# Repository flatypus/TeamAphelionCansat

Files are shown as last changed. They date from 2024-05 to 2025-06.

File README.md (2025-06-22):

# Team Aphelion CanSat | 🏆 1st Place in Canada 2024 | Represented Canada at European Space Agency

## Project repo for Eric Hamber Secondary School from Vancouver, Canada.
### 





### Team Members:
- [Jason Huang](https://www.linkedin.com/in/jason-huang-342449250/) - Co-Captain and Lead Engineer
  - Electrical Design Lead
  - PCB Design and Assembly
  - Mechanical Design and Fabrication
  - CanSat Integration
- [Tristan Yan-Klassen](https://www.linkedin.com/in/tristan-yan-klassen-510788275/) - Co-Captain and Mission Leader
  - Mechanical Design and Fabrication Lead
  - Drilling Apparatus Design and Assembly
  - CanSat Body and Systems Integration
- [Hinson Chan](https://github.com/flatypus) - Software Lead
  - Ground Station Software
  - Map Library Development
  - Website Development
- [John Xu](https://youtube.com/@ibuildstuff) - Hardware Lead
  - Landing Apparatus
  - Soil Sample Intake
  - Ground Station Hardware
- [Anthony Lu](https://www.linkedin.com/in/anthony-lu-026628241/) - External Communications
  - Outreach
  - Parachute Testing
- Mendel Rieseberg - Ground Control
  - Radio Communications

### Project abstract

The goal of CanSat is to design and build a small satellite that fits inside a 330mL soda can. The satellite will be launched to an altitude of 1km and will be deployed to land safely on the ground. We must equip the satellite with sensors to measure temperature, pressure, altitude, and location.

### This Repository

The project is split into six subdirectories:
- 'backend': The backend server for the ground station
- 'mission-control': The frontend dashboard for the ground station
- 'landing': The landing page for the website
- 'embedded': The Arduino code for the CanSat microcontroller
- 'electrical': The electrical schematics and PCB manufacturing files
- 'mechanical': The CAD files of our CanSat

The embedded code consists of sensors detecting temperature, pressure, altitude, and location. The data is sent to the ground station via radio communication, which is relayed via socket communication to the frontend dashboard. The dashboard then visualizes that information in the form of graphs, a map showing the CanSat's location, and the live 3D rotation of the CanSat.

## Project Presentation

This CanSat is designed to complete the primary mission, which is to send temperature and pressure data to the ground station live, at least once a second via radio. The CanSat also has a secondary mission, which is to drill into soil, take a soil sample, and test it with a ninhydrin chemical test within the CanSat's internal chamber. Using the CanSat's FPV live camera, we will determine the presence of amino acids in the soil if a change of color is shown in the ninhydrin.

To accomplish this, the CanSat will be first launched in a rocket to around 1km, then deployed with a parachute to descend at around 6m/s. When the CanSat lands, it will be on its side; we will send a command through our ground station to release the landing legs, which will spring the CanSat upright. We will then initiate the drill, which will drill a hole through our waterproof water chamber, releasing the water onto the soil to dampen it. The CanSat will then continue drilling into the soil, picking up a sample of wet soil, and then stop drilling and retracting up into the CanSat body. The ninhydrin chamber will swivel into place, where then the drill will lower into the chemical, allowing the soil to begin the chemical test. All of this will be remotely controlled from our dashboard.

### Mechanical Design
- Designed in SolidWorks and 3D printed by Tristan, Jason, and John. 
- Custom drill bit and other parts machined to fit inside the CanSat body.
- 4 motors used: GB 2208 Gimbal motor for drilling, 5g servo for testing chamber, N20 worm gear motor for leg release, and 2.5g servo for lead screw.



### Custom Designed Printed Circuit Board
- Designed and hand-assembled by Jason on KiCad.
- Onboard sensors: GPS, 6 axis IMU, and 2 redundant barometers.
- Includes MOSFETs for motor control, 5V buck converter, and TVS diodes for ESD protection.



### Software/Ground Control
- CanSat onboard programming written in Arduino
  - Written for Teensy 4.0, so it supports 'multithreading' (with careful process jumping)
- Nextjs frontend + ExpressJS backend, written by Hinson
  - Data path: Onboard sensors -> Arduino serial -> Radio -> WebSocket backend -> Nextjs graph
- Graphs showing live data updates (temperature, pressure, calculated altitude)
- Fully-functional offline (no WIFI) slippy map
  - Open-sourced [here](https://github.com/flatypus/react-offline-maps) and [npm](https://www.npmjs.com/package/react-offline-maps)
  - You can also embed it as a react component with `bun i react-offline-maps`
  - OSM tile layers; tile caching
- Gyrometer data 3D (threejs)
- Control motors live with Bidirectional communication
  - Buttons send message via. data path in reverse:
  -  Websockets -> Radio -> Serial read -> parse as commands -> send power to pin



### Cost Breakdown


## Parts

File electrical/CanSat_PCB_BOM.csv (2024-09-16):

Reference | Value | Datasheet | Footprint | Qty | Cost/Unit | Total Cost
C1,C3,C4 | 22u | ~ | Capacitor_SMD:C_0805_2012Metric | 3 | 0.349 | 1.047
C2,C5,C6,C7,C8,C9,C10,C11,C12 | 100n | ~ | Capacitor_SMD:C_0603_1608Metric | 9 | 0.0936 | 0.8424
D1,D2 | B260S1F-7 | https://www.diodes.com/assets/Datasheets/B260S1F.pdf | Diode_SMD:D_SOD-123F | 2 | 0.4 | 0.8
D7, D8, D9, D12 | ESD24VLB-TP | https://www.mccsemi.com/pdf/Products/ESD24VLB(DFN1006-2).pdf | Diode_SMD:D_SOD-882 | 4 | 0.37 | 1.48
D3,D4,D5,D6,D10,D11,D13 | D5V0F1U2LP-7B | https://www.diodes.com/assets/Datasheets/D5V0F1U2LP.pdf | Diode_SMD:D_SOD-882 | 7 | 0.297 | 2.079
J1 | Radio Connector | ~ | Connector_JST:JST_GH_SM04B-GHS-TB_1x04-1MP_P1.25mm_Horizontal | 1 | 0.65 | 0.65
J2,J3,J4 | Servo Connector | ~ | Connector_JST:JST_GH_SM03B-GHS-TB_1x03-1MP_P1.25mm_Horizontal | 3 | 0.601 | 1.803
J5 | Drill Motor Connector | ~ | Connector_JST:JST_GH_SM03B-GHS-TB_1x03-1MP_P1.25mm_Horizontal | 1 | 0.601 | 0.601
J6 | 17V Mosfet Connector | ~ | Connector_JST:JST_GH_SM02B-GHS-TB_1x02-1MP_P1.25mm_Horizontal | 1 | 0.66 | 0.66
J7 | 5V Mosfet Connector | ~ | Connector_JST:JST_GH_BM02B-GHS-TBT_1x02-1MP_P1.25mm_Vertical | 1 | 0.61 | 0.61
J8 | Batt Connector | ~ | Connector_JST:JST_XH_S2B-XH-A-1_1x02_P2.50mm_Horizontal | 1 | 0.28 | 0.28
J9 | LED Connector | ~ | Connector_JST:JST_GH_SM02B-GHS-TB_1x02-1MP_P1.25mm_Horizontal | 1 | 0.66 | 0.66
L1 | 4.7u | https://search.murata.co.jp/Ceramy/image/img/P02/J(E)TE243A-9104.pdf | Inductor_SMD:L_1210_3225Metric | 1 | 1.24 | 1.24
R1,R2 | 2k2 | ~ | Resistor_SMD:R_0603_1608Metric | 2 | 0.065 | 0.13
R5,R7,R11 | 100R | ~ | Resistor_SMD:R_0603_1608Metric | 3 | 0.065 | 0.195
R3,R4,R6,R8 | 10k | ~ | Resistor_SMD:R_0603_1608Metric | 4 | 0.065 | 0.26
U1 | AP63205WU | https://www.diodes.com/assets/Datasheets/AP63200-AP63201-AP63203-AP63205.pdf | Package_TO_SOT_SMD:TSOT-23-6 | 1 | 1.34 | 1.34
U2 | BMP390 | https://www.bosch-sensortec.com/media/boschsensortec/downloads/datasheets/bst-bmp390-ds002.pdf | BMP390:10LGA_2X2X0p75_BOS | 1 | 6.38 | 6.38
U3 | BMI088 | https://www.bosch-sensortec.com/media/boschsensortec/downloads/datasheets/bst-bmi088-ds001.pdf | BMI088:QFN_BMI085_BOS | 1 | 11.36 | 11.36
U4 | MS5611-01BA | https://www.te.com/commerce/DocumentDelivery/DDEController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 | Package_LGA:LGA-8_3x5mm_P1.25mm | 1 | 18.07 | 18.07
U5 | SAM-M10Q-00B | https://content.u-blox.com/sites/default/files/documents/SAM-M10Q_DataSheet_UBX-22013293.pdf | SAM_M10Q_00B:XCVR_SAM-M10Q-00B | 1 | 48.78 | 48.78
U6 | Teensy 4.0 | https://www.pjrc.com/store/teensy40.html | Teensy 4.0:MODULE_DEV-15583 | 1 | 36.3 | 36.3
U7,U8 | BSR802NL6327HTSA1 | https://www.infineon.com/dgdl/BSR802N_Rev2.1.pdf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 | BSR802 MOSFET:PG-SC59_INF | 2 | 0.55 | 1.1
Pin Header | 14 pos |  |  | 2 | 0.74 | 1.48
Pin Header | 5 pos |  |  | 1 | 0.18 | 0.18
Total |  |  |  |  |  | 138.33

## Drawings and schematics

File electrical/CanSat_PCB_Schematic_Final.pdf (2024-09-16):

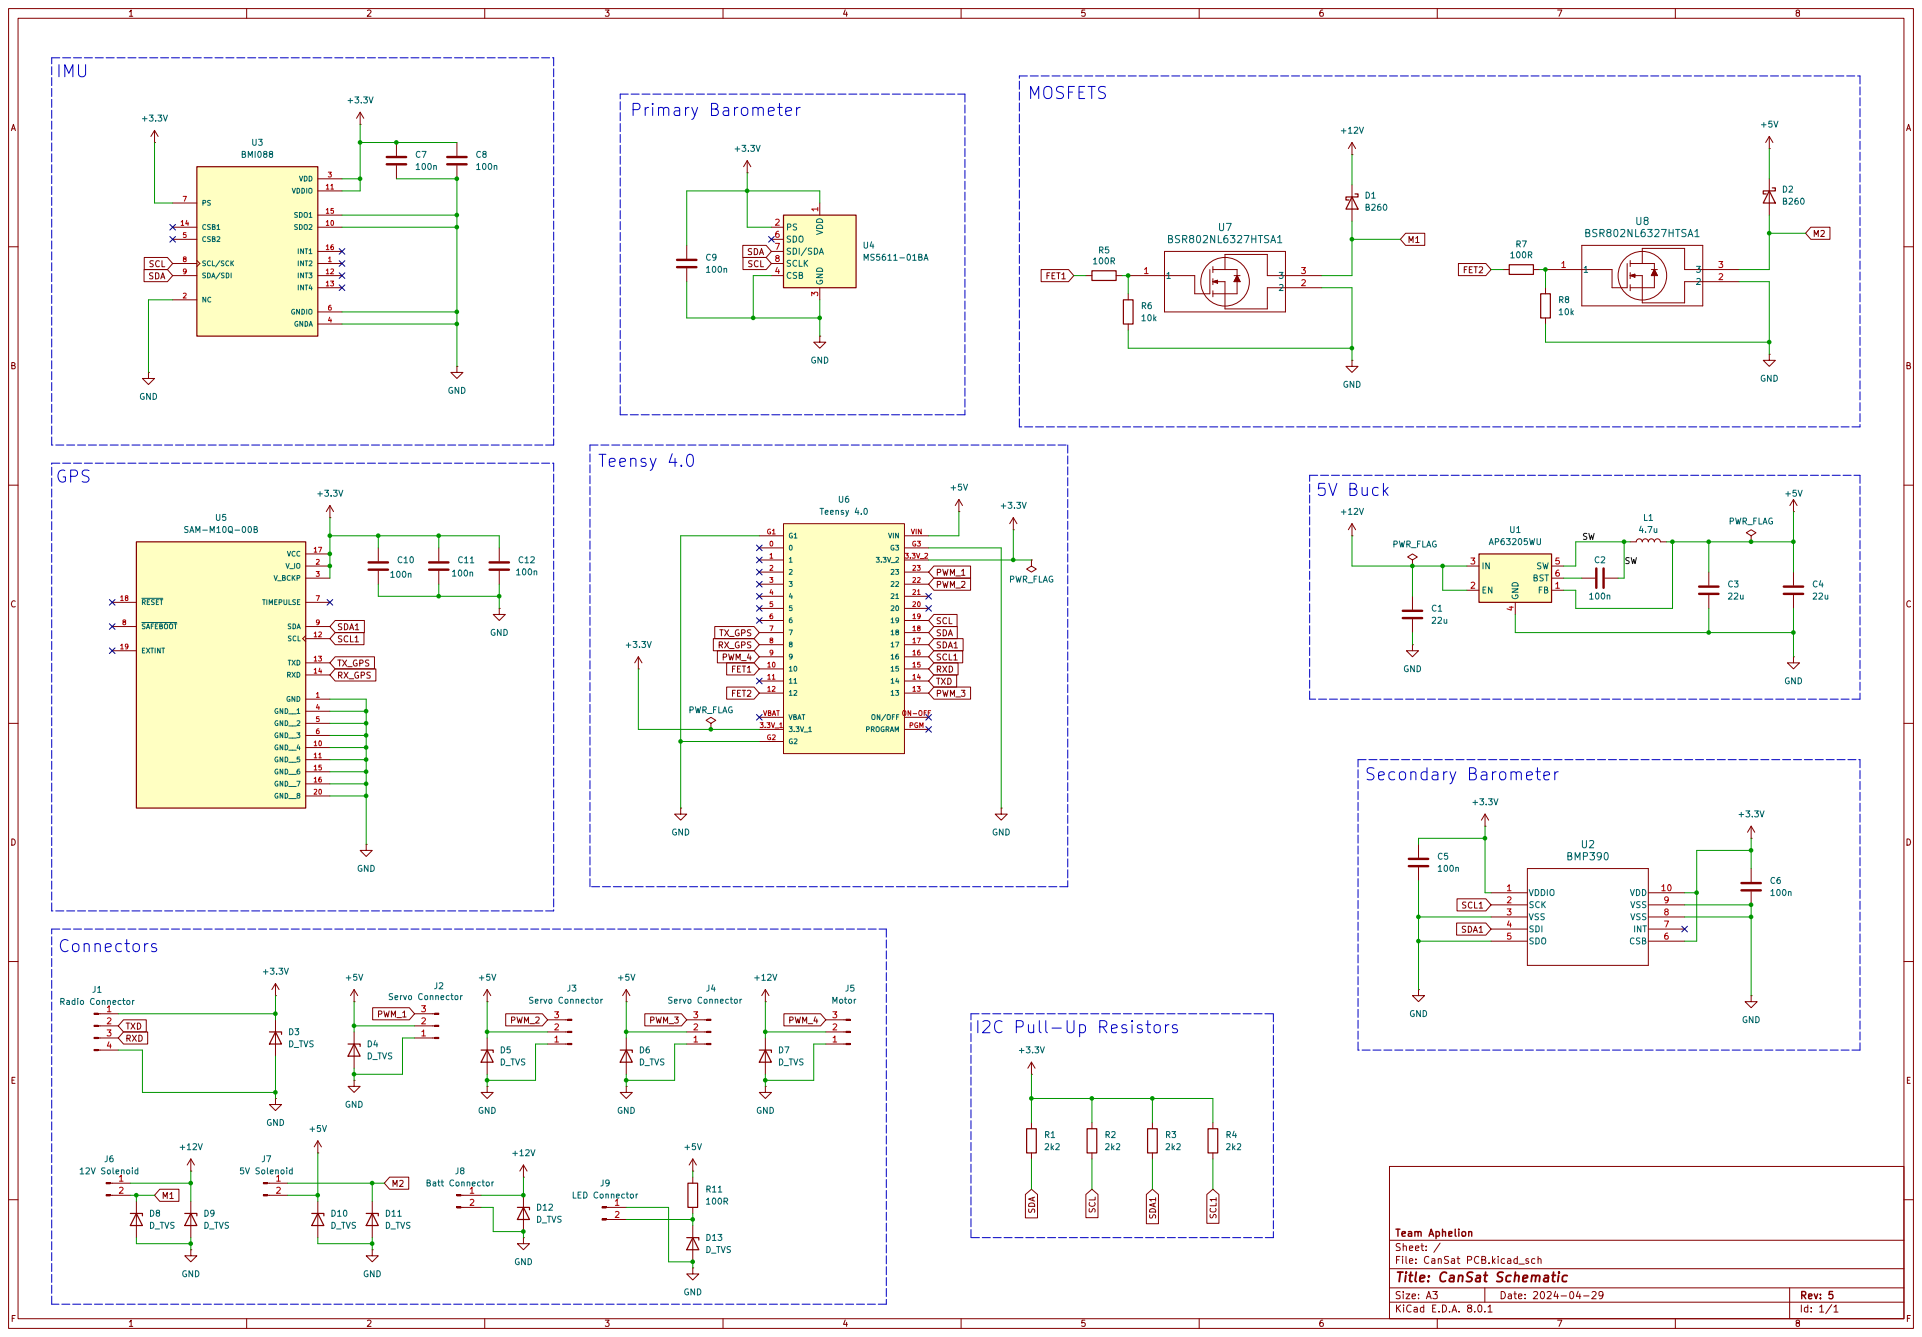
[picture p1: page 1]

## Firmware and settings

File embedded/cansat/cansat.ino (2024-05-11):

#include "BMI088.h"
#include "SoftwareSerial.h"
#include <Filters.h>
#include <Filters/Butterworth.hpp>
#include <MS5611.h>
#include <PWMServo.h>
#include <Servo.h>
#include <SparkFun_u-blox_GNSS_v3.h>
#include <SPI.h>
#include <TeensyThreads.h>
#include <Wire.h>

PWMServo tankServo; // create servo object to control a servo
PWMServo verticalServo;
Servo drill;

#pragma region SensorObjects
SoftwareSerial loraSerial(15, 14);
MS5611 sensor;
SFE_UBLOX_GNSS GPSGNSS;
Bmi088 bmi(Wire, 0x18, 0x68);
#pragma endregion

#define GPSWire Wire1
#define gnssAddress 0x42

float referencePressure;
float referenceAltitude;

long BAUD_RATE = 57600;

// magic numbers for the butterworth filter
const float f_s = 100;
const float f_c = 40;
const float f_n = 2 * f_c / f_s;
auto filter = butter<6>(f_n);

#pragma region GlobalVariables
volatile int realTemperature;
volatile int rawPressure;
volatile int realPressure;
volatile int realAltitude;
volatile int relativeAltitude;
volatile int accelX;
volatile int accelY;
volatile int accelZ;
// volatile int gyroX = 0;
// volatile int gyroY = 0;
// volatile int gyroZ = 0;
volatile int gyroVelX = 0;
volatile int gyroVelY = 0;
volatile int gyroVelZ = 0;
volatile int latitude = 0;
volatile int longitude = 0;
volatile int confirmation = 0;
#pragma endregion

Threads::Mutex lora_lock;

int factor = 1000;

void mainSensorThread()
{
  while (1)
  {
    sensor.read();
    bmi.readSensor();

    realTemperature = sensor.getTemperature() * factor;
    float localPressure = sensor.getPressure();
    rawPressure = localPressure * factor;
    float localRealPressure = filter(localPressure);
    realPressure = localRealPressure * factor;
    float localRealAltitude = altitude(localRealPressure);
    realAltitude = localRealAltitude * factor;
    relativeAltitude = (localRealAltitude - referenceAltitude) * factor;
    accelX = bmi.getAccelX_mss() * factor;
    accelY = bmi.getAccelY_mss() * factor;
    accelZ = bmi.getAccelZ_mss() * factor;
    gyroVelX = bmi.getGyroX_rads() * factor;
    gyroVelY = bmi.getGyroY_rads() * factor;
    gyroVelZ = bmi.getGyroZ_rads() * factor;

    delay(1);
  }
}

void gpsThread()
{
  while (1)
  {
    if (GPSGNSS.getPVT())
    {
      latitude = GPSGNSS.getLatitude();
      longitude = GPSGNSS.getLongitude();
    }
    delay(1);
  }
}

void executeCommand(int command)
{
  int position;
  switch (command)
  {
  case 0: // Move drill up
    verticalServo.write(160);
    break;
  case 1: // Hold drill
    verticalServo.write(100);
    break;
  case 2: // Move drill down
    verticalServo.write(30);
    break;
  case 3: // Drill start
    position = drill.readMicroseconds();
    if (position != 1000)
      return;
    for (int i = 0; i < 7; i++)
    {
      drill.writeMicroseconds(1300 + i * 100);
      delay(1000);
    }
    break;
  case 4: // Drill stop
    drill.writeMicroseconds(1000);
    break;
  case 6: // Rest chamber
    tankServo.write(133);
    break;
  case 7: // Water chamber
    tankServo.write(81);
    break;
  case 8: // Test chamber
    tankServo.write(60);
    break;
  case 9: // FPV ON
    digitalWrite(12, HIGH);
    break;
  case 10: // FPV OFF
    digitalWrite(12, LOW);
    break;
  case 11: // Landing legs
    digitalWrite(10, HIGH);
    delay(100);
    digitalWrite(10, LOW);
    break;
  default:
    Serial.println("Unknown command");
    break;
  }
}

void read()
{
  char data[255];
  int i = 0;

  if (loraSerial.available())
  {
    while (loraSerial.available())
    {
      data[i] = loraSerial.read();
      i++;
    }
    int command = parseMessage(data);
    if (command != -1)
    {
      Serial.print("[Recieved]: ");
      Serial.println(command);
      executeCommand(command);
      confirmation = 1;
    }
  }
}

void setup()
{
  Serial.begin(BAUD_RATE);
  loraSerial.begin(BAUD_RATE);
  Wire.begin();
  GPSWire.begin();
  verticalServo.attach(22);
  tankServo.attach(23);
  pinMode(10, OUTPUT);
  pinMode(12, OUTPUT);
  drill.attach(9, 1000, 2000);
  drill.writeMicroseconds(1000);
  delay(500);
  drill.writeMicroseconds(1100);
  delay(1000);
  drill.writeMicroseconds(1000);

  while (!loraSerial.isListening())
  {
    Serial.println("LoRa is not listening!! Check something");
    delay(1000);
  }
  Serial.println("LoRa is listening!");

  while (!sensor.begin())
  {
    Serial.println("ms5611 not found, check wiring!");
    delay(1000);
  }
  Serial.println("ms5611 found!");

  while (GPSGNSS.begin(GPSWire, gnssAddress) == false)
  {
    Serial.println(F("u-blox GNSS not detected. Retrying..."));
    delay(1000);
  }
  Serial.println("GNSS module detected!");

  while (bmi.begin() < 0)
  {
    Serial.println("BMI Initialization Error");
    delay(1000);
  }
  Serial.println("BMI Initialized!");

  sensor.read();
  referencePressure = sensor.getPressure();
  referenceAltitude = altitude(referencePressure);
  sensor.setOversampling(OSR_ULTRA_HIGH);
  GPSGNSS.setI2COutput(COM_TYPE_UBX);

  threads.addThread(mainSensorThread);
  threads.addThread(gpsThread);
}

void println(const char *data)
{
  threads.suspend(1);
  threads.suspend(2);
  int dataLength = strlen(data);
  char *str = (char *)malloc(15 + dataLength + (dataLength / 10));
  sprintf(str, "AT+SEND=69,%d,%s", dataLength, data);
  Serial.print("[Sending]: ");
  Serial.println(str);
  loraSerial.println(str);
  free(str);
  threads.restart(1);
  threads.restart(2);
}

void loop()
{
  for (int i = 0; i < 10; i++)
  {
    if (confirmation == 1)
    {
      break;
    }
    read();
    delay(50);
  }

  char buffer[255];
  sprintf(
      buffer,
      "%i,%i,%i,%i,%i,%i,%i,%i,%i,%i,%i,%i",
      realTemperature, realPressure, realAltitude, relativeAltitude, latitude, longitude, accelX, accelY, accelZ, gyroX, gyroY, gyroZ);

  if (confirmation == 1)
  {
    confirmation = 0;
    delay(250);
  }

  println(buffer);
}

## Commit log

2024-04-07 feat: moved landing
2024-05-04 feat: velocity zooming
2024-05-09 feat: threading
2024-05-09 fix: clean up some stuff
    [cansat.ino]
2024-05-09 fix: finally multithreading works
    [cansat.ino]
2024-05-09 feat: drilling
2024-05-10 feat: added additional features for cansat mission_control - FPV camera on-off - Landing legs open - Drill motor runs - Labelling command buttons
2024-09-10 feat: gerbers
    [CanSat PCB-B_Cu.gbr, CanSat PCB-B_Mask.gbr, CanSat PCB-B_Paste.gbr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]
2024-09-10 feat: schematic and image
2024-09-11 refactor: renamed folder from gerbers to electrical
    [CanSat PCB-B_Cu.gbr, CanSat PCB-B_Mask.gbr, CanSat PCB-B_Paste.gbr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]
2024-09-16 Added PCB files
    [CanSat PCB-B_Cu.gbr, CanSat PCB-B_Mask.gbr, CanSat PCB-B_Paste.gbr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]
2024-09-18 Uploaded all CAD files
2024-09-18 Uploaded SolidWorks assembly file
